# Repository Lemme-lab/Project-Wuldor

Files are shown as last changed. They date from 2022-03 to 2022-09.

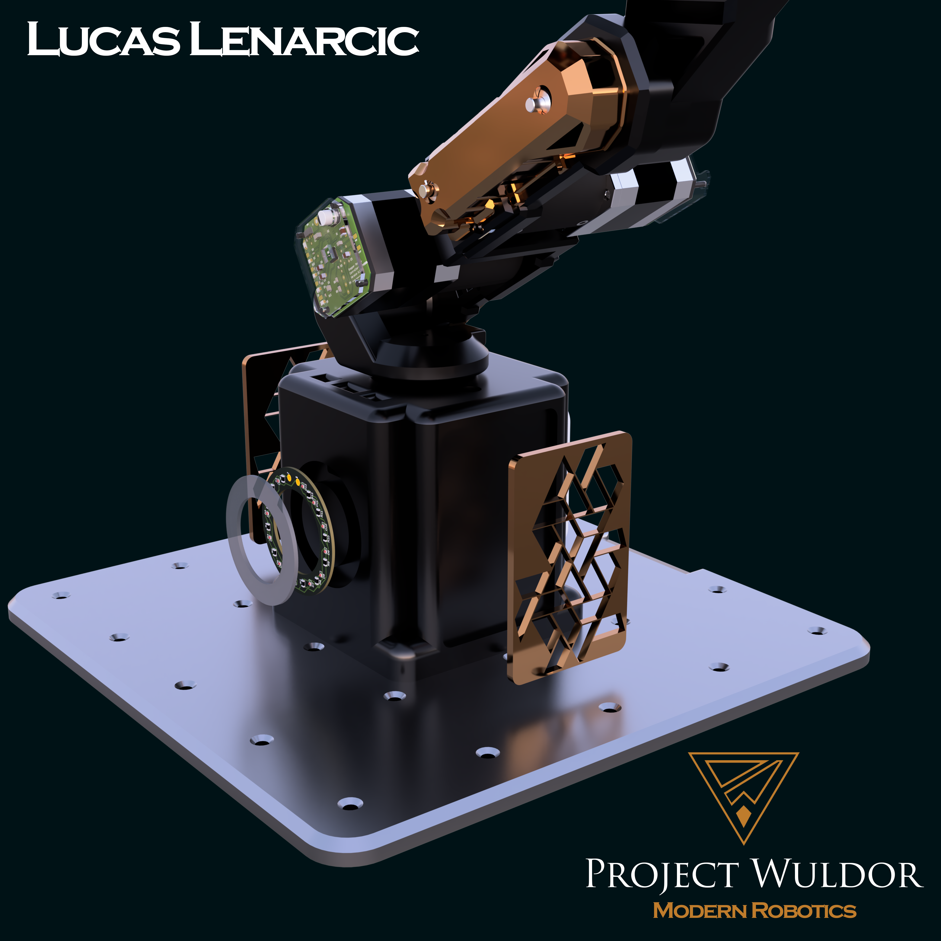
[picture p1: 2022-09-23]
Images/Assembly Led Ring - Base.png

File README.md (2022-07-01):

# Project Wuldor
---
## A completely custom 6 Axis Roboter-Arm (Still in progress) that won the 2022 HTL Mössingerstraße Technicus Award. 
---

---
Banner
---
unnamed
---
Packaging_Arm
---
Packaging_PCB's
---
PCB-Display
---

---
3D-Modell_2022-Mar-06_03-12-34PM-000_CustomizedView13790056020_mp4 (1)
---

## Features 
- Self Designed Stepper Motor Controller (A4988) 
- Self designed Main Controller with a small footprint
- Compact Size Factor
- Esthetic 
- Many other little Features

---
Main_PCB_Renders
---
Stepper_motors_driver_renders
---

## Planned Code:
### General:  
A few bullet points and explanations for the code part. Different technologies and programming languages such as C++, WEB-Dev, and Flutter will be used. It will go from Basic C and register manipulation to UI-Development on Cross-Platform Mobile Apps.  
  
- Controlling Axis 1- 5  
- Save Control sequence  
- Remote  Connection  
- Desktop  Application  
- Website  
- Mobile App  
- PHP Database  
- C++, HTML, CSS, JS, FLUTTER, JAVA, Python
- Tensorflow, Keras

---
  
### Website:  
An HTML Website that must be functional and appealing to use. Features will be send via a ESP32 and the included Wireless module. Cross-platform Data will mean that we will have to save the current data and inputs on a small database. UI and other Features will mean that we have to use JS with or without an additional framework.  
 --- 
Website-Wuldor
 --- 
- Checking Power Status  
- Check Wireless Connection  
- Current Voltage/Power Levels  
- Slider  Controlls for Motors  
- Test Motor func  
- Switch Mode (Normal Control, Train ,AI)  
- Cam Live Stream implementation  
- Stop/Start/hold -->pan> Slide buttons  
- Speed  
- Axis coordinates  
  
--- 
  
### Desktop Client  
A C++ or Java desktop client to be used when wired up to the robot arm. From the User ready interface to debbuging, testing and programming features will be included. This is one of the most important interface to the robot arm and as such it will be programmed first.  
  
- Checking Power Status  
- Check Wireless Connection  
- Current Voltage/Power Levels  
- Slider  Controlls for Motors  
- Test Motor func  
- Switch Mode (Normal Control,AI)  
- Cam  
- Debug Features / Console  
- Test  Features  
- Stop/Start/Hold -->  slidebuttons  
- Speed  
  
--- 
  
### Mobile Client  
Last we will do a Mobile Client app for controlling and checking the robot arm on the go. It will be programmed in Flutter or another Mobile Cross Platform Developer Kit.
--- 
  App-Prototype
---   
- Checking Power Status  
- Check Wireless Connection  
- Current-Voltage/Power Levels  
- Settings  
- Live Cam   

---

### Self-Test
Testclasses to exclude code-mistakes. Motors are working in the corract way and also the remote connection and controlling from the web applicatio, if so then we can put everything together and test the whole thing

- Motor
- Remote Connection
- Connections Seriell/Connectors 
  
---
### Currently in Work
---
IN_WORK
---
The whole code will be versioned via GIT, inputs to the Roboter Arm tested, and the whole project will be publicly available on GitHub.
---
https://trello.com/b/jWCULnX8
---

## Stepper Motor + Reducer
17HS4401 v4
---
17HS15-1684S-HG100 v7
---
11HS20-0674S-PG51 v3

------

## Stepper Motor Controller 

------

------

------
SteppperController pdf_v1_2022-Apr-15_08-58-34AM-000_CustomizedView13134334629_png_alpha
SteppperController pdf_v1_2022-Apr-15_08-48-39AM-000_CustomizedView932799733_png_alpha
------

## Main Controller

------

------
Main_Controller pdf_2022-Apr-15_07-07-20AM-000_CustomizedView21684845978_png_alpha
Main_Controller pdf_2022-Apr-15_07-34-52AM-000_CustomizedView14152361556_png_alpha
------
3D-Modell_2022-Jan-30_05-11-22PM-000_CustomizedView10729507097_png_alpha

------

## Roboter-Arm
---
Assemlby Bottom
---
Assembly Arm 2
---
Assembly Gripper
---
View Arm 3-4-5
---
Assembly Led Ring - Base
---

------

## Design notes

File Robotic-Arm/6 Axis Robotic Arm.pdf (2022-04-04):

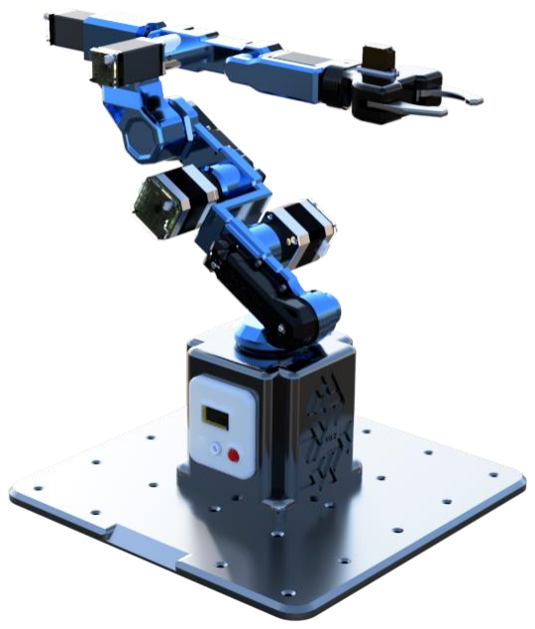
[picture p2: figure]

NAME | Lucas-Elias Lenarcic | STUNDEN | GEFEHLT
KLASSE | | DATUM
WERKSTÄTTE | | KAL. WOCHE
LEHRER | Prof. Grabner Burkhard | SEITE | GEPRÜFT

# 6 Axis Robotic Arm Technicus Award '22

### GitHub: https://github.com/Lemme-lab/Robotic-Arm

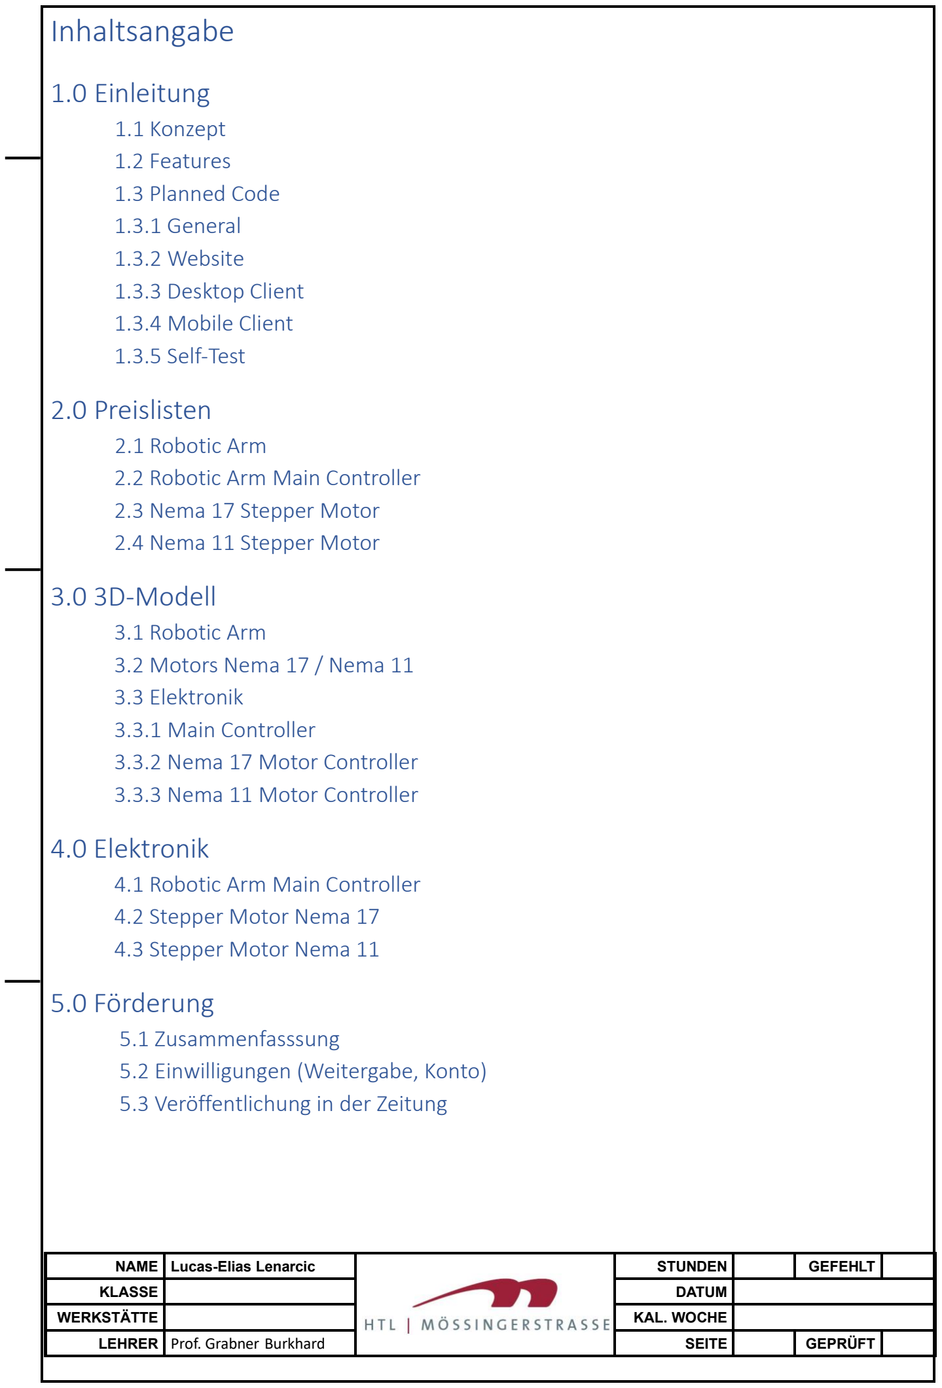
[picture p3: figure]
KLASSE; DATUM; WERKSTÄTTE; KAL. WOCHE; Inhaltsangabe; 1.0 Einleitung; 1.1 Konzept 1.2 Features 1.3 Planned Code 1.3.1 General 1.3.2 Website 1.3.3 Desktop Client 1.3.4 Mobile Client 1.3.5 Self-Test; 2.0 Preislisten; 2.1 Robotic Arm 2.2 Robotic Arm Main Controller 2.3 Nema 17 Stepper Motor 2.4 Nema 11 Stepper Motor; 3.0 3D-Modell; 3.1 Robotic Arm 3.2 Motors Nema 17 / Nema 11 3.3 Elektronik 3.3.1 Main Controller 3.3.2 Nema 17 Motor Controller 3.3.3 Nema 11 Motor Controller; 4.0 Elektronik; 4.1 Robotic Arm Main Controller 4.2 Stepper Motor Nema 17 4.3 Stepper Motor Nema 11; 5.0 Förderung; 5.1 Zusammenfasssung 5.2 Einwilligungen (Weitergabe, Konto) 5.3 Veröffentlichung in der Zeitung

NAME | Lucas-Elias Lenarcic | STUNDEN | GEFEHLT

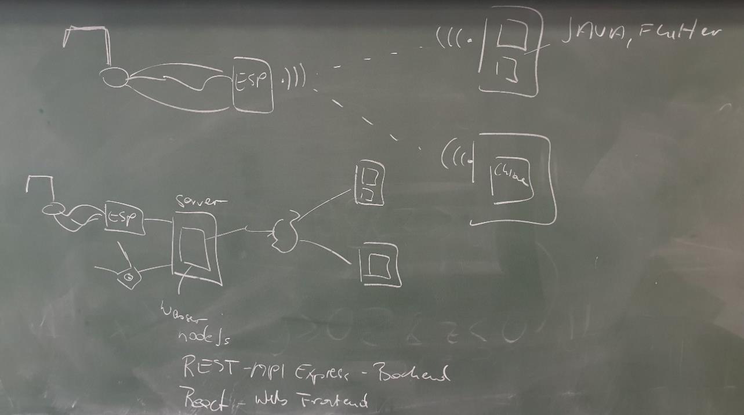
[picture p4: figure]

NAME | Lucas-Elias Lenarcic | STUNDEN | GEFEHLT
KLASSE | | DATUM
WERKSTÄTTE | | KAL. WOCHE

## 1.0 Einleitung

1.1 Konzept
Für den Technicus Award der HTL, haben wir (Lucas Lenarcic und Matteo Müller) uns,
im Zuge des Werkstättenunterrichts bei Herrn Prof. Grabner Burkhard, überlegt einen 6-Achsen Roboterarm zu bauen.

Der Roboterarm wurde/wird mithilfe von Fusion entworfen. Die einzelnen mechanischen Komponenten des Armgehäuses werden mithilfe eines 3D-Druckers gefertigt. Elektronische Komponenten, wie Motortreiber, Stromversorgung, Steuerung via App oder Web wurden/werden mit der PCB-Design Software Altium entworfen. Für die Herstellung dieser Platinen wird entweder die schulinterne Leiterplattenfertigung hinzugezogen oder ein externer Hersteller.

Es ist geplant mit dem Greifer des Roboterarms Objekte aufzuheben und diese an einem beliebigen, in der Reichweite des Armes gelegenen, Punkt wieder abzulegen.
Die Steuerung soll wie in den folgenden Punkten noch genauer beschrieben über mehrere Varianten möglich gemacht werden.

So soll man den Roboter mithilfe einer Webapplikation, also über eine selbst designte HTML-Website (virtueller Joystick, …) und folglich mit dem ESP32 und dessen eingebautem WLAN-Modul steuern können.
Die andere Variante wäre bzw. ist eine App, die wir mithilfe von Flutter designen werden.

NAME | Lucas-Elias Lenarcic | STUNDEN | GEFEHLT
KLASSE | | DATUM
WERKSTÄTTE | | KAL. WOCHE

1.2 Features

- Self Designed Stepper Motor Controller (A4988)
- Self designed Main Controller with a small footprint
- Compact Size Factor
- Esthetic
- Many other little Features

1.3 Planned Code:
1.3.1 General:
A few bullet points and explanations for the code part. Different technologies and programming languages such as C++, WEB-Dev, and Flutter will be used. It will go from Basic C and register manipulation to UI-Development on Cross-Platform Mobile Apps.
- Controlling Axis 1- 5
- Save Control sequence
- Remote Connection
- Desktop Application
- Website
- Mobile App
- PHP Database
- C++, HTML, CSS, JS, FLUTTER, JAVA, Python
- Tensorflow, Keras

NAME | Lucas-Elias Lenarcic | STUNDEN | GEFEHLT
KLASSE | | DATUM
WERKSTÄTTE | | KAL. WOCHE

1.3.2 Website:
A HTML Website that must be functional and appealing to use. Features will be send via a ESP32 and the included Wireless module. Cross-platform Data will mean that we will have to save the current data and inputs on a small database. UI and other Features will mean that we have to use JS with or without an additional framework.
- Checking Power Status
- Check Wireless Connection
- Current Voltage/Power Levels
- Slider Controlls for Motors
- Test Motor func
- Switch Mode (Normal Control, Train ,AI)
- Cam Live Stream implementation
- Stop/Start/hold -->pan> Slide buttons
- Speed
- Axis coordinates

1.3.3 Desktop Client
A C++ or Java desktop client to be used when wired up to the robot arm. From the User ready interface to debbuging, testing and programming features will be included. This is one of the most important interface to the robot arm and as such it will be programmed first.
- Checking Power Status
- Check Wireless Connection
- Current Voltage/Power Levels
- Slider Controlls for Motors
- Test Motor func
- Switch Mode (Normal Control,AI)
- Cam
- Debug Features / Console
- Test Features
- Stop/Start/Hold --> slidebuttons
- Speed

NAME | Lucas-Elias Lenarcic | STUNDEN | GEFEHLT
KLASSE | | DATUM
WERKSTÄTTE | | KAL. WOCHE

1.3.4 Mobile Client
Last we will do a Mobile Client app for controlling and checking the robot arm on the go. It will be programmed in Flutter or another Mobile Cross Platform Developer Kit.
- Checking Power Status
- Check Wireless Connection
- Current-Voltage/Power Levels
- Settings
- Live Cam

1.4.5 Self-Test
Testclasses to exclude code-mistakes. Motors are working in the corract way and also the remote connection and controlling from the web applicatio, if so then we can put everything together and test the whole thing
- Motor
- Remote Connection
- Connections Seriell/Connectors

## 2.0 Preislisten

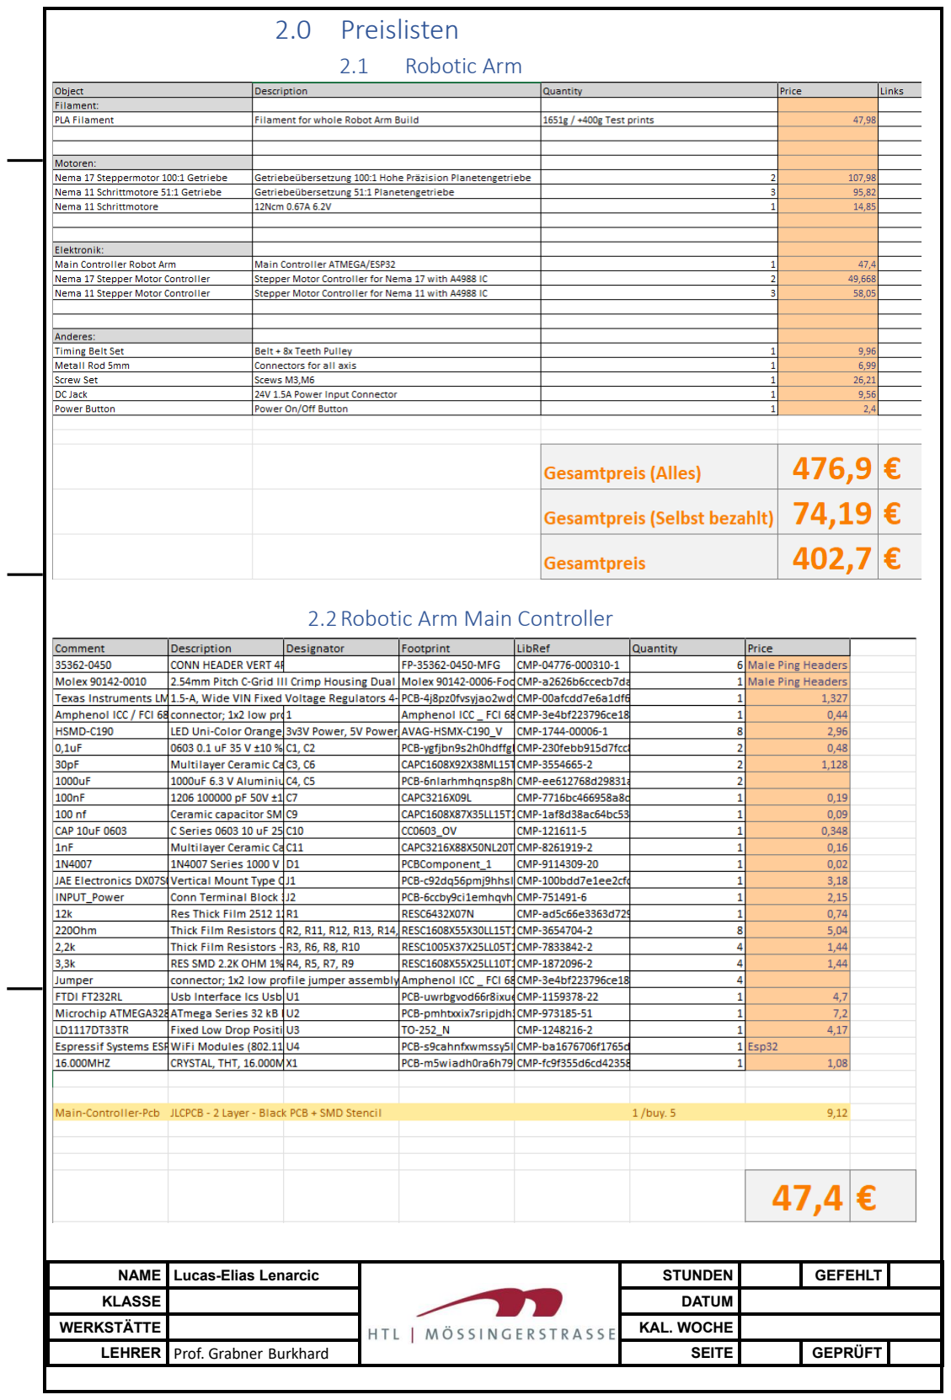
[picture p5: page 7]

NAME | Lucas-Elias Lenarcic | STUNDEN | GEFEHLT
KLASSE | | DATUM
WERKSTÄTTE | | KAL. WOCHE
2.1 | Robotic Arm

2.2Robotic Arm Main Controller

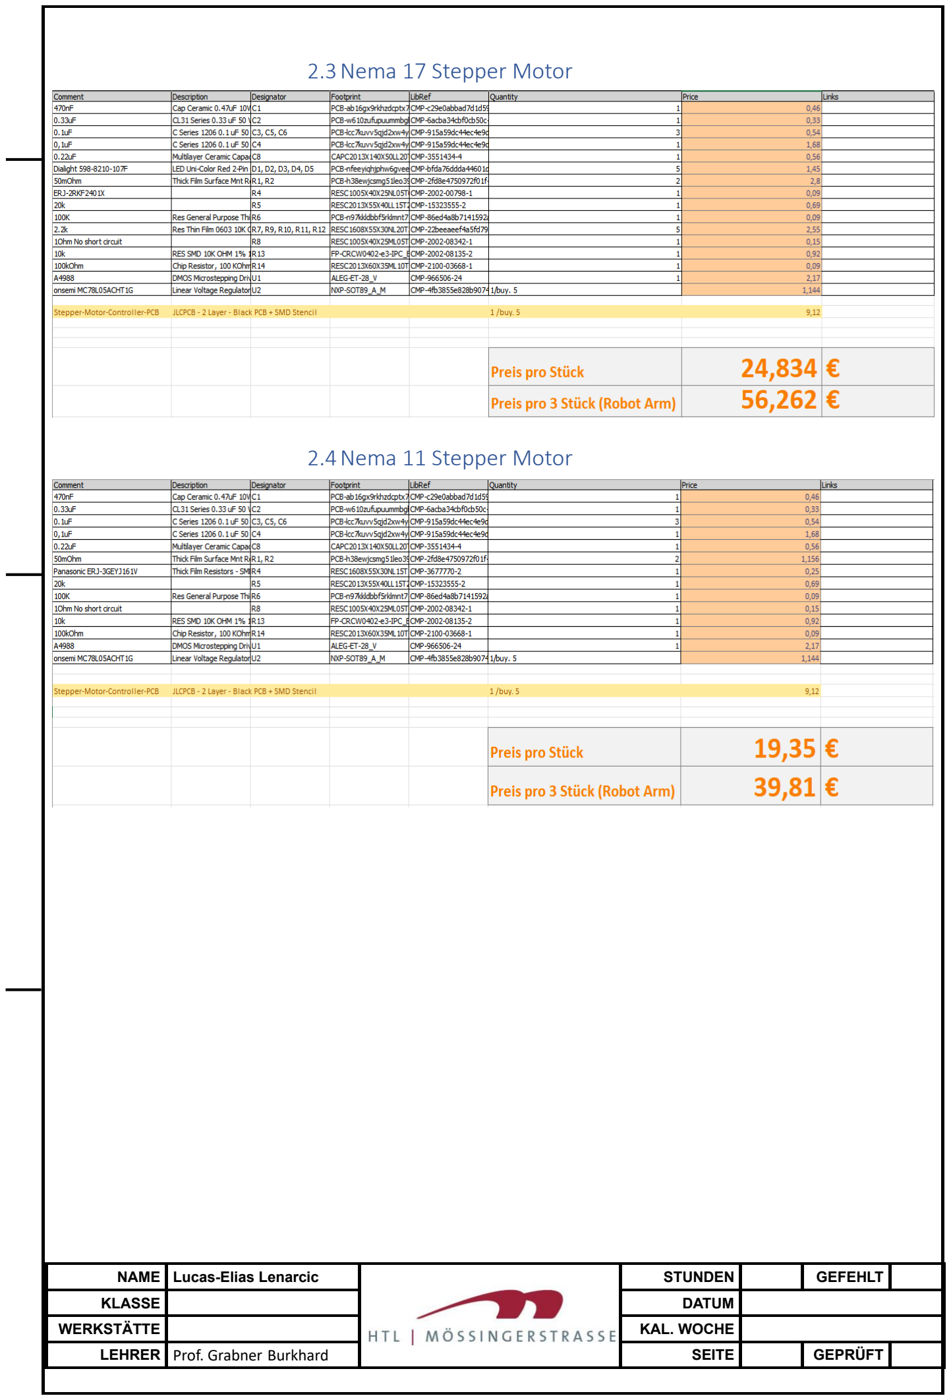
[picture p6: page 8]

NAME | Lucas-Elias Lenarcic | STUNDEN | GEFEHLT
KLASSE | | DATUM
WERKSTÄTTE | | KAL. WOCHE

2.3Nema 17 Stepper Motor

2.4Nema 11 Stepper Motor

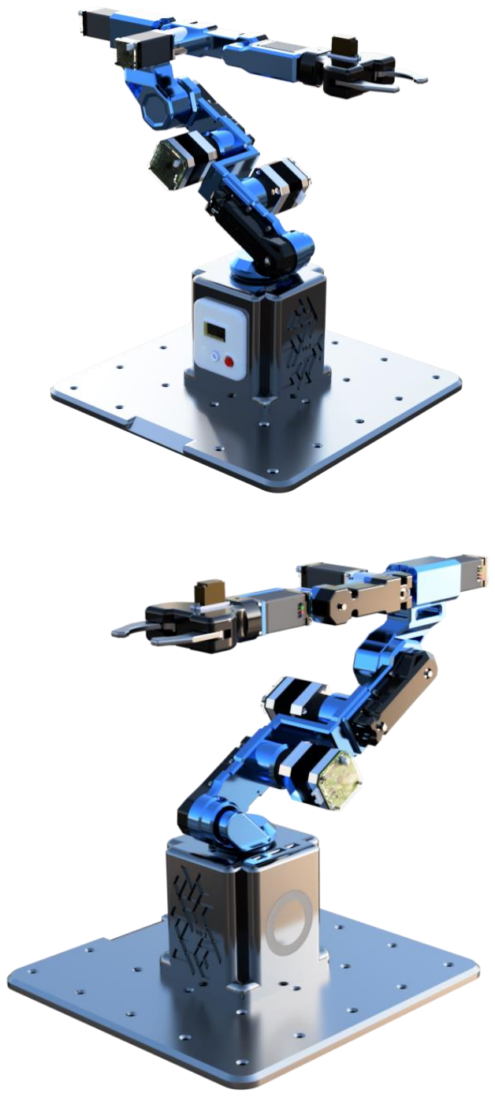
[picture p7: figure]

NAME | Lucas-Elias Lenarcic | STUNDEN | GEFEHLT
KLASSE | | DATUM
WERKSTÄTTE | | KAL. WOCHE

## 3.0 3D-Modells

3.1 Robotic Arm

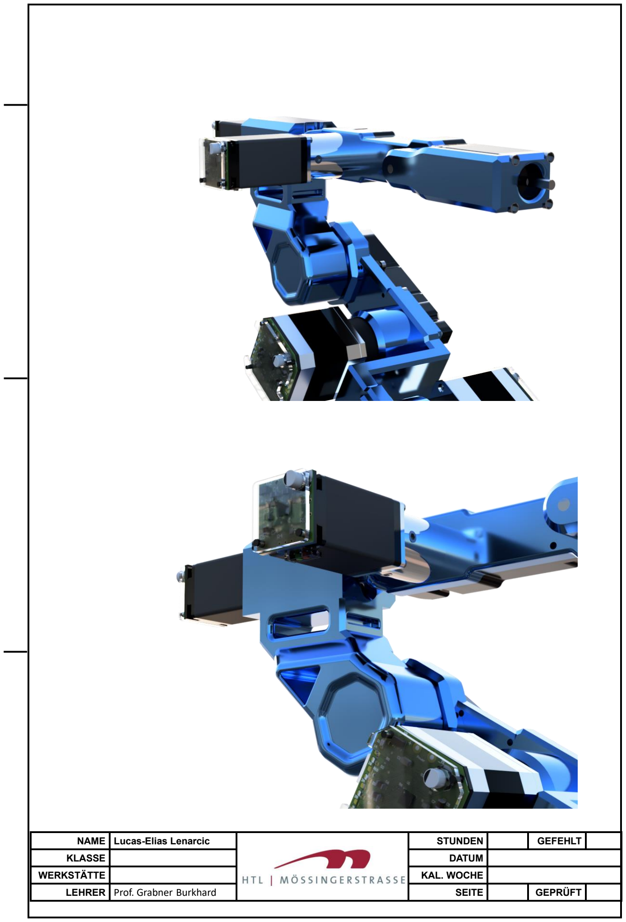
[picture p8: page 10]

NAME | Lucas -Elias Lenarcic | STUNDEN | GEFEHLT
KLASSE | | DATUM
WERKSTÄTTE | | KAL. WOCHE

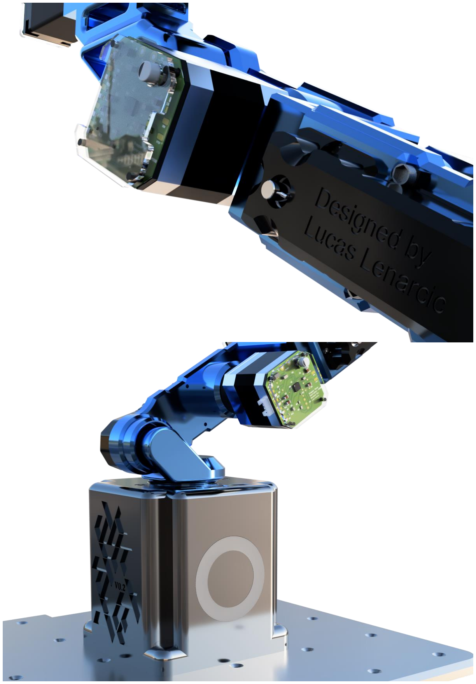
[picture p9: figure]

NAME | Lucas -Elias Lenarcic | STUNDEN | GEFEHLT
KLASSE | | DATUM
WERKSTÄTTE | | KAL. WOCHE

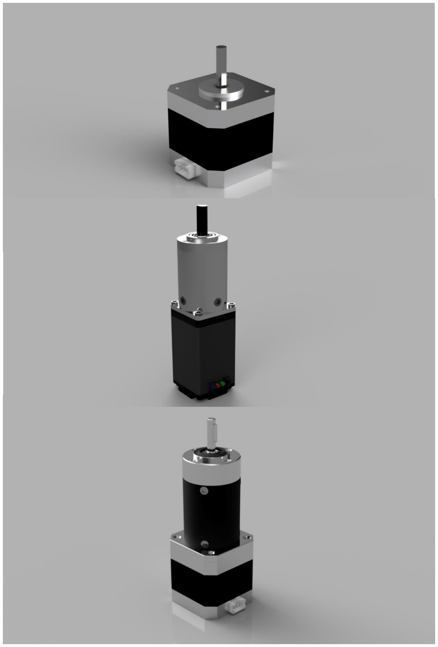
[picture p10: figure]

NAME | Lucas-Elias Lenarcic | STUNDEN | GEFEHLT
KLASSE | | DATUM
WERKSTÄTTE | | KAL. WOCHE

3.2 Motors Nema 17 / Nema 11

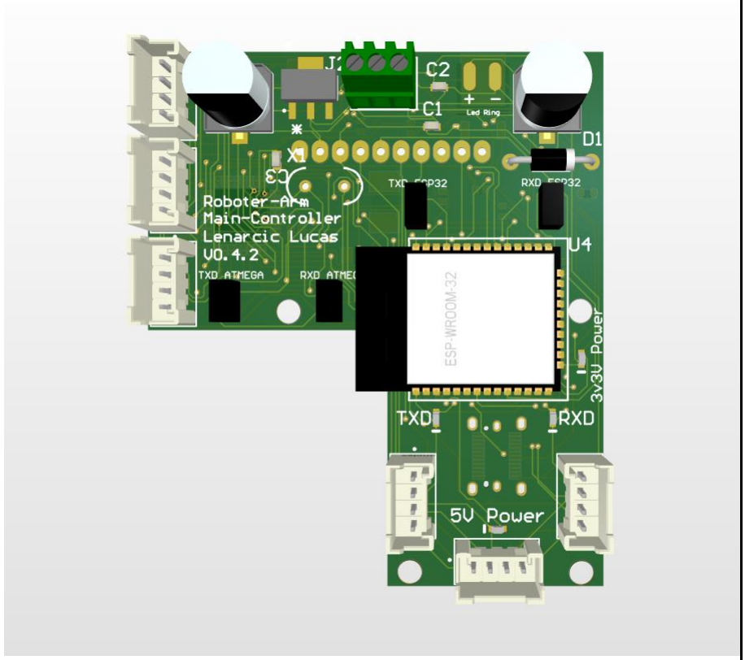
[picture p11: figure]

NAME | Lucas-Elias Lenarcic | STUNDEN | GEFEHLT
KLASSE | | DATUM
WERKSTÄTTE | | KAL. WOCHE

3.3Elektronik
3.3.1 Main Controller:

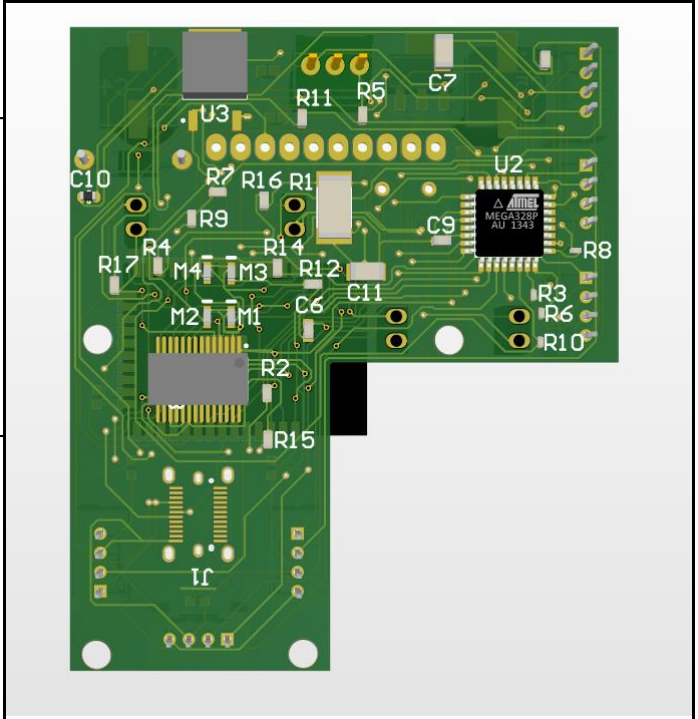
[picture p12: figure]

NAME | Lucas -Elias Lenarcic | STUNDEN | GEFEHLT
KLASSE | | DATUM
WERKSTÄTTE | | KAL. WOCHE

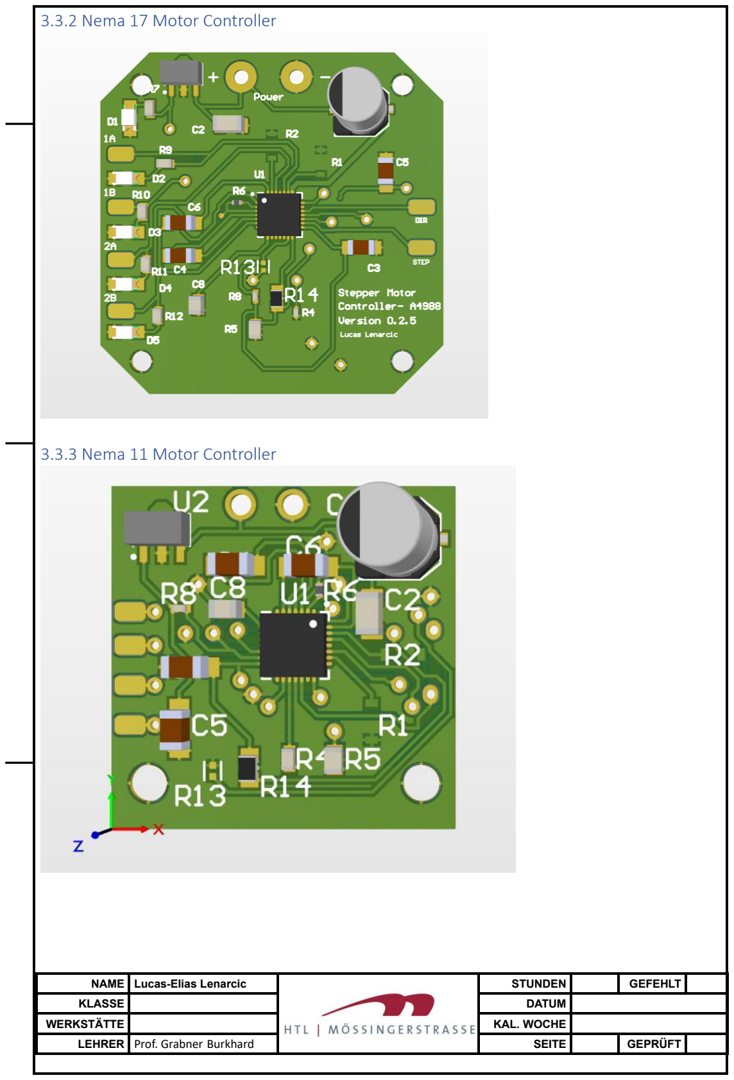
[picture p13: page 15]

NAME | Lucas-Elias Lenarcic | STUNDEN | GEFEHLT
KLASSE | | DATUM
WERKSTÄTTE | | KAL. WOCHE

3.3.2 Nema 17 Motor Controller

3.3.3 Nema 11 Motor Controller

## 4.0 Elektronik

## 4.1 Robotic Arm Main Controller

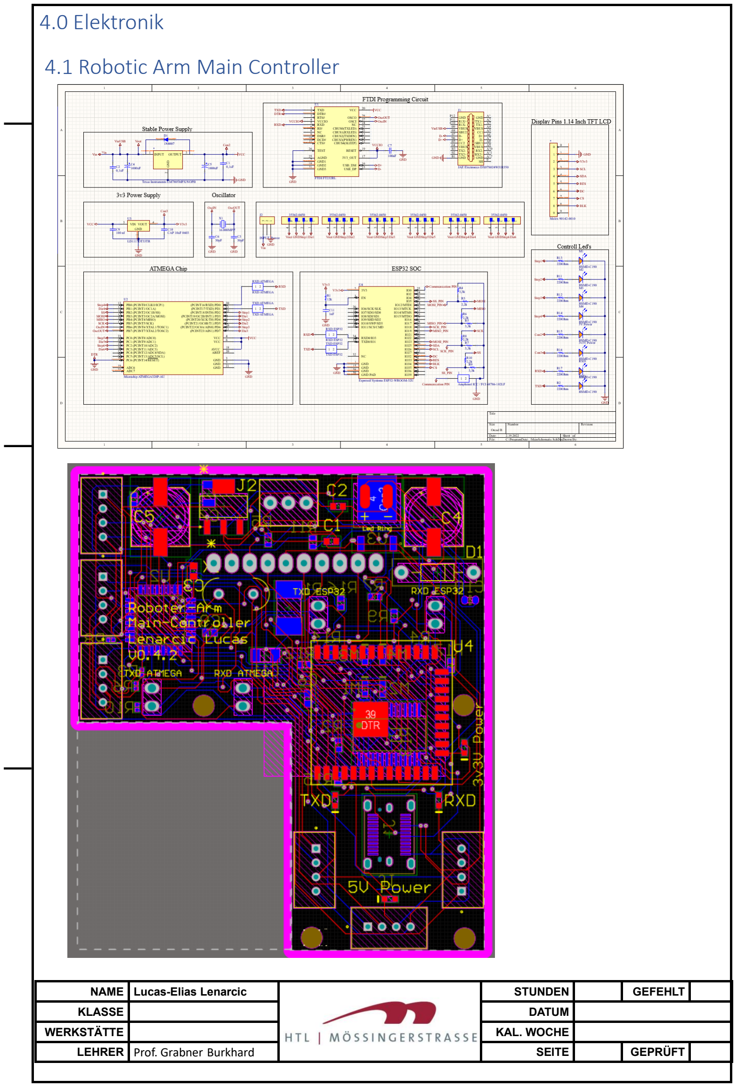
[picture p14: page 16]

NAME | Lucas-Elias Lenarcic | STUNDEN | GEFEHLT
KLASSE | | DATUM
WERKSTÄTTE | | KAL. WOCHE

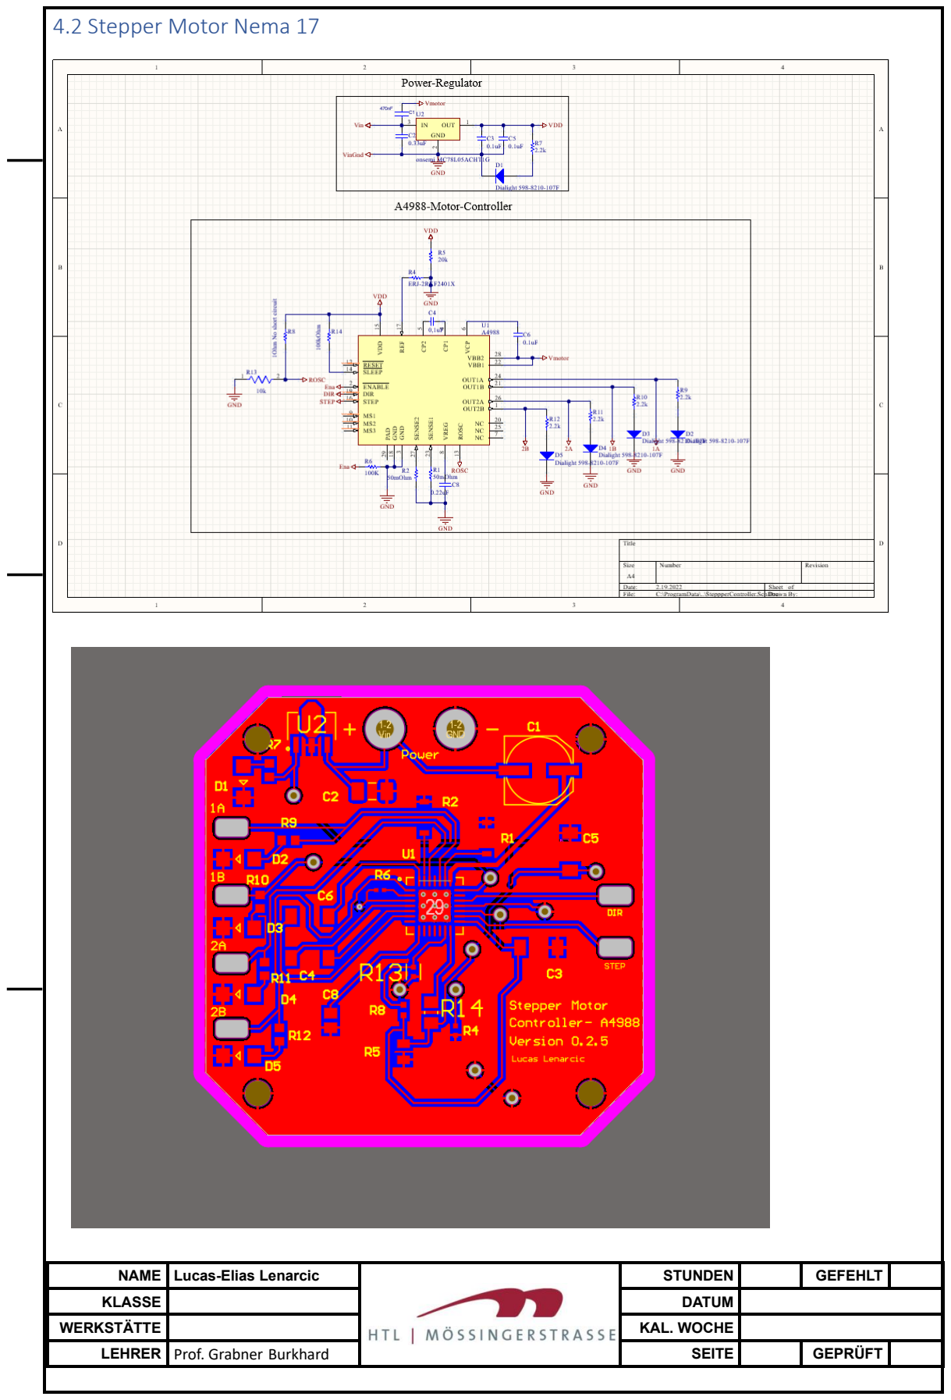
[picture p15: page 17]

NAME | Lucas-Elias Lenarcic | STUNDEN | GEFEHLT
KLASSE | | DATUM
WERKSTÄTTE | | KAL. WOCHE

4.2 Stepper Motor Nema 17

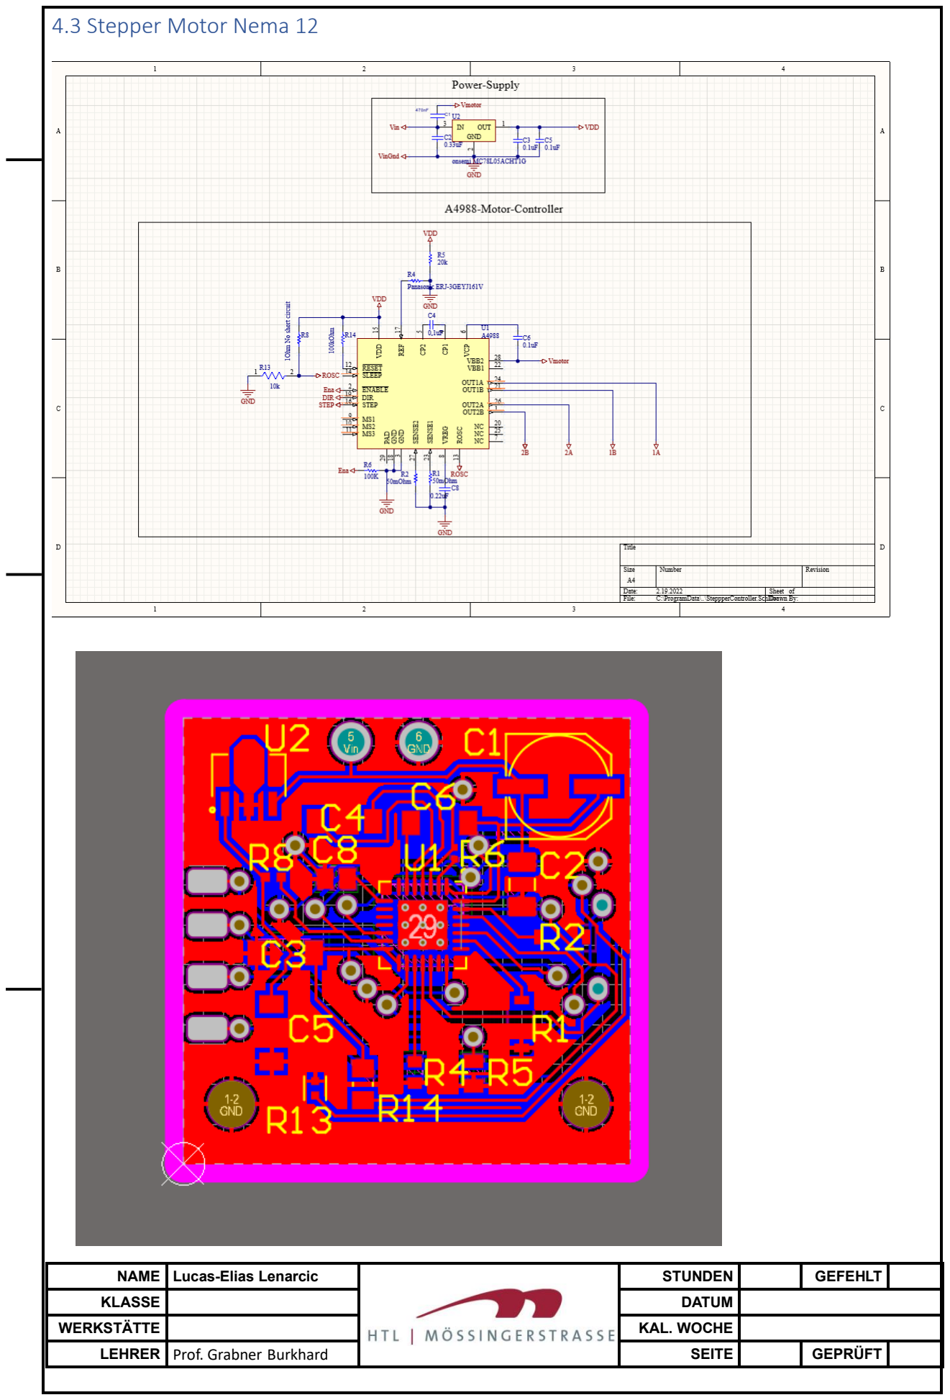
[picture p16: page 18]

NAME | Lucas-Elias Lenarcic | STUNDEN | GEFEHLT
KLASSE | | DATUM
WERKSTÄTTE | | KAL. WOCHE

4.3 Stepper Motor Nema 12

NAME | Lucas-Elias Lenarcic | STUNDEN | GEFEHLT
KLASSE | | DATUM
WERKSTÄTTE | | KAL. WOCHE

## 5.0 Förderung

5.1 Zusammenfasssung

Für den Technicus Award der HTL, haben wir (Lucas Lenarcic und Matteo Müller) uns,
im Zuge des Werkstättenunterrichts bei Herrn Prof. Grabner Burkhard, überlegt einen 6-Achsen Roboterarm zu bauen.

Der Roboterarm wurde/wird mithilfe von Fusion entworfen. Die einzelnen mechanischen Komponenten des Armgehäuses werden mithilfe eines 3D-Druckers gefertigt. Elektronische Komponenten, wie Motortreiber, Stromversorgung, Steuerung via App oder Web wurden/werden mit der PCB-Design Software Altium entworfen. Für die Herstellung dieser Platinen wird entweder die schulinterne Leiterplattenfertigung hinzugezogen oder ein externer Hersteller.

Es ist geplant mit dem Greifer des Roboterarms Objekte aufzuheben und diese an einem beliebigen, in der Reichweite des Armes gelegenen, Punkt wieder abzulegen.
Die Steuerung soll wie in den folgenden Punkten noch genauer beschrieben über mehrere Varianten möglich gemacht werden.

So soll man den Roboter mithilfe einer Webapplikation, also über eine selbst designte HTML-Website (virtueller Joystick, …) und folglich mit dem ESP32 und dessen eingebautem WLAN-Modul steuern können. Die andere Variante wäre bzw. ist eine App, die wir mithilfe von Flutter designen werden.

- Self Designed Stepper Motor Controller (Nema 17, Nema 11) (A4988)
- Self designed Main Controller (ATMEGA, ESP32, USB-C Interface, Display, Power Reg.)
- Different Interfaces (Controlling)
- Compact size factor of Electronics and Modell
- Esthetic appealing Modells, Interfaces and Electronics
- Many other little Features

Website:
A HTML Website that must be functional and appealing to use. Features will be send via a ESP32 and the included Wireless module. Cross-platform Data will mean that we will have to save the current data and inputs on a small database. UI and other Features will mean that we have to use JS with or without an additional framework.

Desktop Client
A C++ or Java desktop client to be used when wired up to the robot arm. From the User ready interface to debbuging, testing and programming features will be included. This is one of the most important interface to the robot arm and as such it will be programmed first.

Mobile Client
Last we will do a Mobile Client app for controlling and checking the robot arm on the go. It will be programmed in Flutter or another Mobile Cross Platform Developer Kit.

NAME | Lucas-Elias Lenarcic | STUNDEN | GEFEHLT
KLASSE | | DATUM
WERKSTÄTTE | | KAL. WOCHE

Eine Erklärung des Antragstellers, wie oft bereits Förderungen beim ABSVB beantragt, und und an ihn ausgezahlt wurden.
- Es wurden keine Anträge vor diesem beantragt und es wurden dadurch auch keine Fördergelder ausgezahlt.

Die saldierten Rechnungen der getätigten Ausgaben (als Original ), bis zum zu fördernden Betrag sind beizulegen (Motto: Keine Förderung ohne bezahlte Rechnung)!.

- Die Bauteile werden erst bestellt, wenn uns Förderungen zu diesem Projekt zugesagt werden. Die Rechnungen werden dann sofort nachgereicht. Alle Preislisten sind beigelegt.

5.2 Einwilligungen (Weitergabe, Konto)

Die Erklärung, dass sie/er damit einverstanden ist, dass der ABSVB die Arbeit für eigene Zwecke verwendet und verwertet. Die Weitergabe an SchülervertreterInnen zur Vervielfältigungen wird ausdrücklich gestattet.

- Antragsteller: _____________________________

Bei mehreren VerfasserInnen eine schriftliche Erklärung aller VerfasserInnen, dass sie mit der Überweisung auf das genannte Konto einverstanden sind.

Ich Matteo Müller bin einverstanden das die Überweisung der Fördergelder auf das Bankkonto
IBAN: AT76 2070 6045 0053 5861 geht.
- Matteo Müller: _____________________________

5.3 Veröffentlichung in der Zeitung

Bei Förderung von Projekten / Arbeiten, ist für die Veröffentlichung in der Zeitung des ABSVBs ein Projektbericht mit projektbezogenem Bild beizulegen (Jeweils als Datei (*.doc, *.jpg), für die EDV mäßige Weiterverarbeitung)!

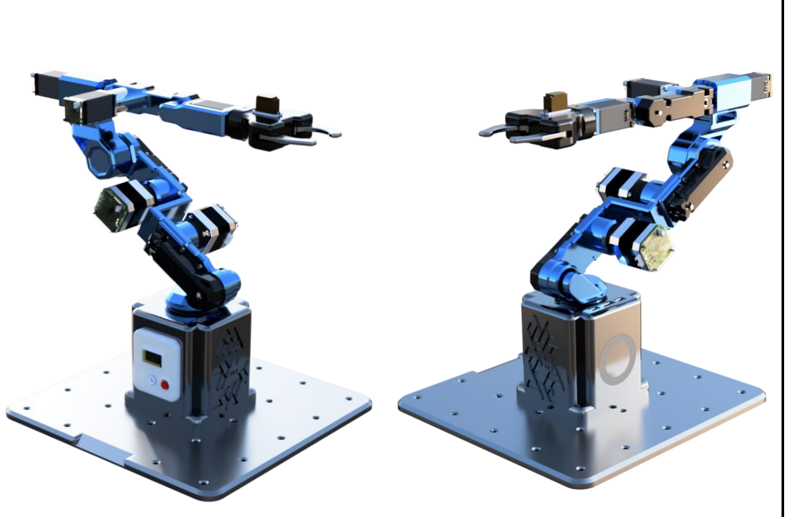
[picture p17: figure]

NAME | Lucas-Elias Lenarcic | STUNDEN | GEFEHLT
KLASSE | | DATUM
WERKSTÄTTE | | KAL. WOCHE

# Robotic-Arm Technicus Award

Für den Technicus Award der HTL, haben wir (Lucas Lenarcic und Matteo Müller) uns, im Zuge des Werkstättenunterrichts bei Herrn Prof. Grabner Burkhard, überlegt einen 6-Achsen Roboterarm zu bauen. Das Projekt wurde durch einen beträchtlich Teil vom Absolventenverband der HTL‘s Klagenfurt gefördert.

Alle Komponenten des Roboterarms werden/wurden von uns selbst entworfen. Me-chanische Bauteile wie das Gehäuse werden mittels 3D-Drucker gefertigt und die elektronischen Komponenten, sprich Platinen, mithilfe der Leiterplattenfertigung der Schule oder durch externe Hersteller.

Mit dem Greifer des Roboterarms soll man Objekte aufheben können und diese an einem beliebigen Punkt wieder ablegen.

Die Steuerung soll mithilfe einer Webapplikation, also über eine selbst designte HTML-Website (virtueller Joystick, …) und folglich mit dem ESP32 und dessen eingebautem WLAN-Modul steuerbar sein, ebenso ist eine Steuer-App geplant.

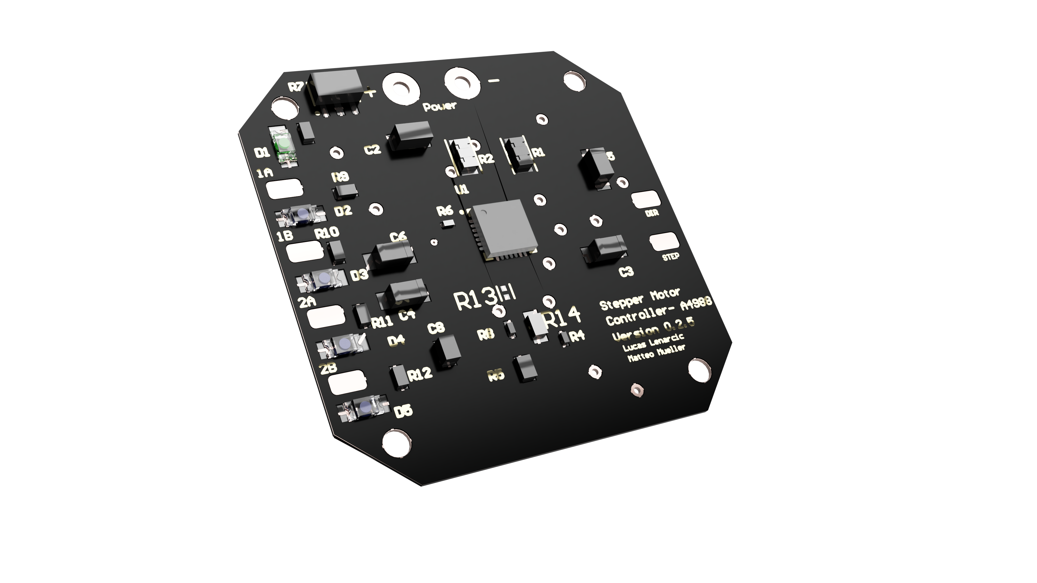
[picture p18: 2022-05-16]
Images/Stepper Controller 1.png

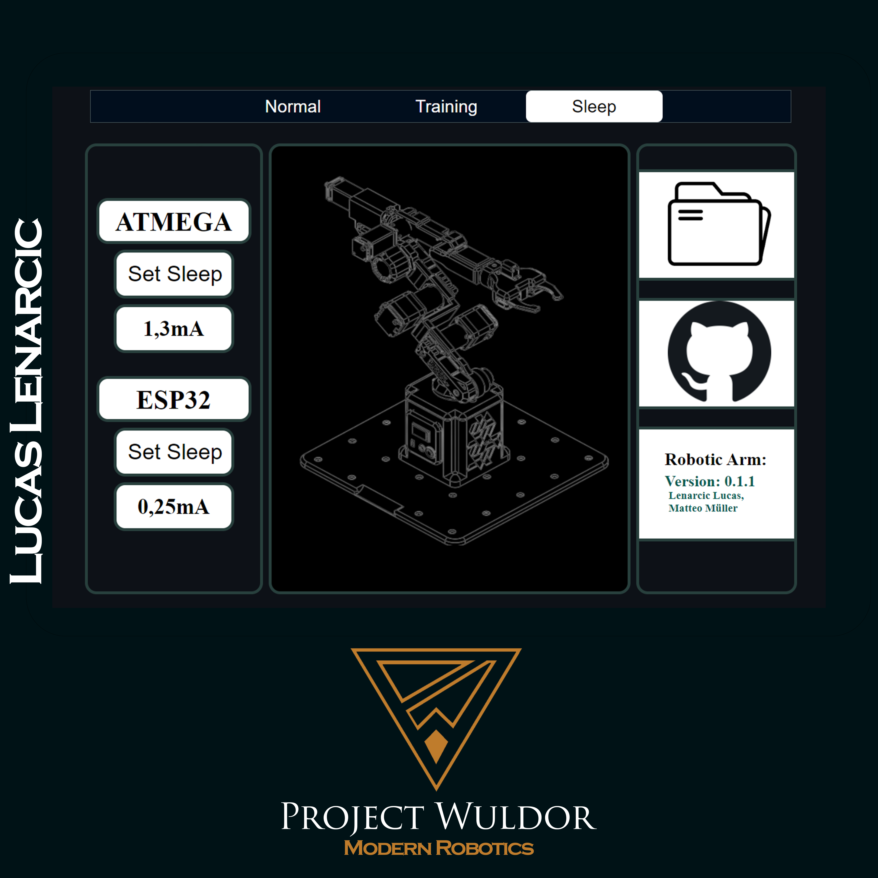
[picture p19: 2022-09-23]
Images/Website-Wuldor.png

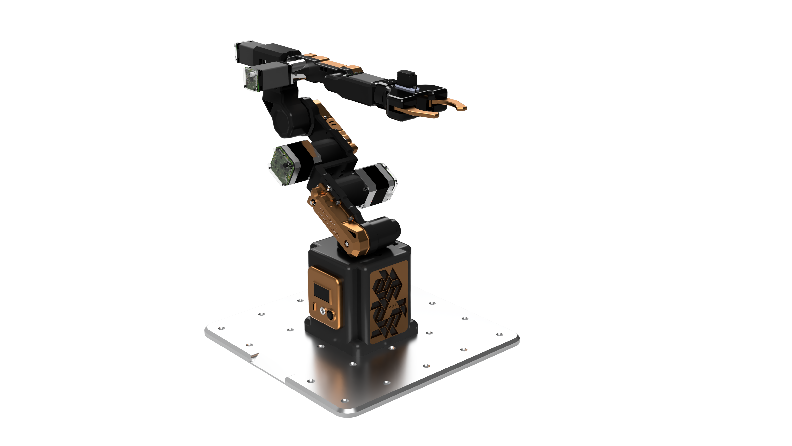
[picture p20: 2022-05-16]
Images/Modell-Copper.png

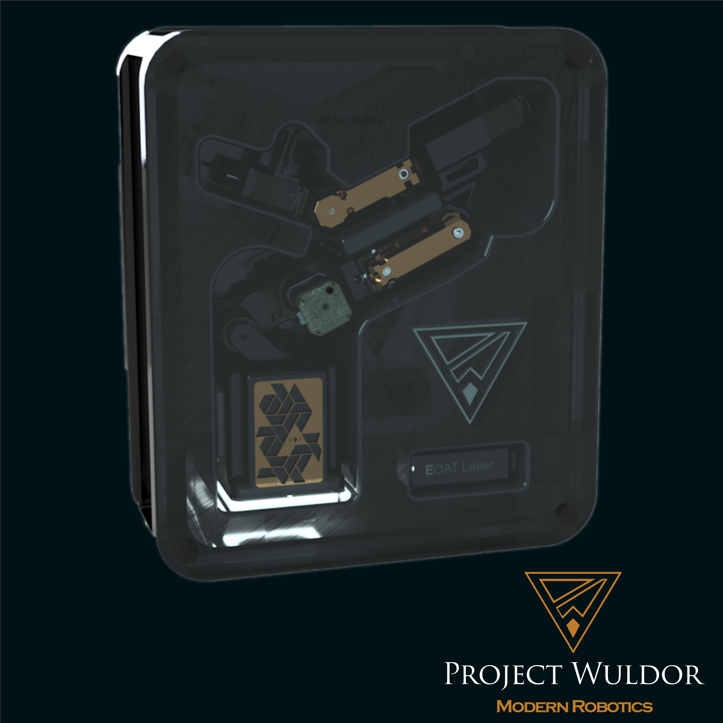
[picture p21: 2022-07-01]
Images/Packaging_Arm_2.png

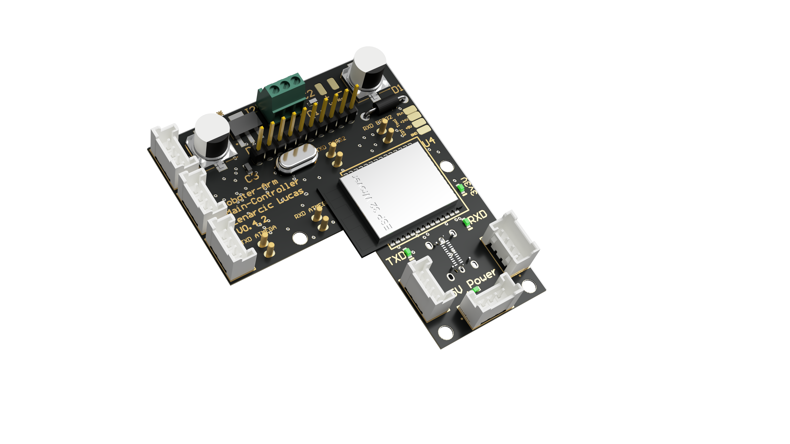
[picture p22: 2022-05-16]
Images/Main Controller 1.png

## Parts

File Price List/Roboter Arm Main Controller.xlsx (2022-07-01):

Comment | Description | Designator | Footprint | LibRef | Quantity
 | Resistance Weld Thru-Hole Crystal, 16 MHz, -20 to 70 degC, 2-Pin THD, RoHS, Bulk |  | FOX-FOXSLF160-20 | CMP-1749-00003-1 | 1
282836-2 | Female Header, Pitch 5 mm, 1 x 2 Position, Height 10 mm, Tail Length 3.5 mm, Rohs, Bulk |  | TECO-282836-2_V | CMP-1684-00017-1 | 1
LD1117DT33TR | Fixed Low Drop Positive Voltage Regulator, 3.3V, 3-Pin DPAK, Tape and Reel | +3V3 | TO-252_N | CMP-0244-00088-1 | 1
LM7805MPX/NOPB | IC REG LINEAR 5V 1.5A SOT223-4 | +5V | FP-LM7805MPX-NOPB-MFG | CMP-04917-000022-1 | 1
 | LED RED CLEAR 0805 SMD | 3V3 Power, 5V Power, EN, Miso, Mosi, RXD, SPI, Step1, Step2, Step3, Step4, TXD | FP-150080SS75000-MFG | CMP-1426-00010-2 | 12
ATmega328P-AU | 8-bit AVR Microcontroller, 32KB Flash, 1KB EEPROM, 2KB SRAM, 32-pin TQFP, Industrial Grade (-40°C to 85°C) | ATMEGA328P | 32A_M | CMP-0095-00269-2 | 1
 | Cap Ceramic 100nF 50V X7R 10% Pad SMD 0603 +125°C Automotive T/R | C1, C4, C5, C6, C9 | FP-CGA3E-0_3-0_1-IPC_A | CMP-2000-07546-2 | 5
 | Aluminum Electrolytic Capacitor, Low Impedance, 1000 uF +/- 20%, 16 V, -55 to 105 degC, 2-Pin 10.3 x 10.3 x 13.5 mm SMD, RoHS, Reel | C2, C3 | NIC-UCL-10x13.5-2_V | CMP-0926-00001-1 | 2
 | CAP CER 30PF 50V 5% NP0 0603 | C7, C8 | FP-C0603C-CF-MFG | CMP-1035-00914-3 | 2
1N4007 | Rectifier diode 1000 V 1 A DO-41, , | D1 | FP-1N4007-MFG | CMP-123542-000001-1 | 1
61300811121 | THT Vertical Pin Header WR-PHD, Pitch 2.54 mm, Single Row, 8 pins | Display | 61300811121 | CMP-1502-01076-1 | 1
ESP32-WROOM-32D | WIFI MODULE 32MBITS SPI FLASH | ESP-32 | FP-ESP32-WROOM-32D-MFG | CMP-194065-000003-1 | 1
FT232RL | IC USB FS SERIAL UART 28-SSOP | FT232RL | FTDI-SSOP-28_M | CMP-2000-05029-1 | 1
 | Male Header, Pitch 2 mm, 1 x 4 Position, Height 6 mm, Tail Length 3.4 mm, -25 to 85 degC, RoHS, Bulk | P1, P2, P3, P4, P5, P6 | JST-B4B-PH-K-S_V | CMP-2000-05165-1 | 6
MMBT2222A-7-F | TRANS NPN 40V 0.6A SMD SOT23-3 | Q1, Q2 | FP-SOT23-IPC_A | CMP-1693-00003-4 | 2
RC0402FR-073K3L |  | R1, R2, R3, R4, R18, R20 | RESC1005X40X25ML05T10 | CMP-2002-07652-1 | 6
RC0603FR-072K2L | Thick Film Resistor, 2.2 KOhm, 100 mW, 50 V, +/- 1%, -55 to 155 degC, 2-Pin SMD (0603), RoHS, Tape and Reel | R5, R6, R7, R8, R17, R19 | RESC1608X55X25LL10T15 | CMP-2000-06934-1 | 6
 | Chip Ferrite Bead, 0603, 220Ω @ 100MHz, 25%, 0.04Ω, 2.5A | R9, R10, R11, R12, R13, R14, R15, R16, R21, R22, R23, R27 | FP-BLM18-0_15-t0_5-MFG | CMP-0686-00596-3 | 12
ERJ3EKF1002V | Chip Resistor, 10 KOhm, +/- 1%, 0.1 W, -55 to 155 degC, 0603 (1608 Metric), RoHS, Tape and Reel | R24, R25 | RESC1609X55X30LL15T15 | CMP-1012-00623-3 | 2
CRCW060312K0FKEA | RES Thick Film, 12kΩ, 1%, 0.1W, 100ppm/°C, 0603 | R26 | FP-CRCW0603-e3-IPC_A | CMP-2000-03877-2 | 1
436333045822 | WS-TASU J-Bend J-Bend SMD Tact Switch with boss design 4.7X3.5 mm side push | Reset | 436333045822 | CMP-1464-00001-1 | 1
RXD ATMEGA | CONN HEADER VERT 2POS 2MM | RXD ATMEGA | FP-M22-2510205-MFG | CMP-15831-000005-1 | 1
RXD ESP32 | CONN HEADER VERT 2POS 2MM | RXD ESP | FP-M22-2510205-MFG | CMP-15831-000005-1 | 1
TXD ESP32 | CONN HEADER VERT 2POS 2MM | TXD ATMEGA, TXD ESP | FP-M22-2510205-MFG | CMP-15831-000005-1 | 2
DX07S024WJ1R350 | No Description Available | USB-C | CONN_DX07S024WJ1R350_JAE | DX07S024WJ1R350 | 1

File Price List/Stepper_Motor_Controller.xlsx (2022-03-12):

Comment | Description | Designator | Footprint | LibRef | Quantity | Price | Links
470nF | Cap Ceramic 0.47uF 10V X5R 20% SMD 0402 85°C T/R | C1 | PCB-ab16gx9rkhzdcptx7kd3-1 | CMP-c29e0abbad7d1d59-2 | 1 | 0.46 | https://www.digikey.at/en/products/detail/0402ZD474MAT2A/478-13018-1-ND/9948536?curr=usd
0.33uF | CL31 Series 0.33 uF 50 V ±10 % Tolerance X7R SMT Multilayer Ceramic Capacitor | C2 | PCB-w610zufupuummbghd1in-1 | CMP-6acba34cbf0cb50c-1 | 1 | 0.33 | https://www.digikey.at/de/products/detail/CL31B334KBFNNNE/1276-1138-1-ND/3889224?curr=eur
0.1uF | C Series 1206 0.1 uF 50 V ±5 % Tolerance C0G SMT Multilayer Ceramic Capacitor | C3, C5, C6 | PCB-lcc7kuvv5qjd2xw4yurg-1 | CMP-915a59dc44ec4e9d-4 | 3 | 0.54 | https://www.digikey.at/de/products/detail/C3216C0G1H104J160AA/445-7694-2-ND/2733129?curr=eur
0,1uF | C Series 1206 0.1 uF 50 V ±5 % Tolerance C0G SMT Multilayer Ceramic Capacitor | C4 | PCB-lcc7kuvv5qjd2xw4yurg-1 | CMP-915a59dc44ec4e9d-4 | 1 | 1.68 | https://www.digikey.at/de/products/detail/C3216C0G1H104J160AA/445-7694-2-ND/2733129?curr=eur
0.22uF | Multilayer Ceramic Capacitors MLCC - SMD/SMT 50volts .22uF 5% X7R 7inch reel | C8 | CAPC2013X140X50LL20T25 | CMP-3551434-4 | 1 | 0.56 | https://at.rs-online.com/web/p/keramik-vielschichtkondensatoren/1441425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
Dialight 598-8210-107F | LED Uni-Color Red 2-Pin Chip 1206(3216Metric) T/R | D1, D2, D3, D4, D5 | PCB-nfeeyiqhjphw6gveeqew-1 | CMP-bfda76ddda44601d-2 | 5 | 1.45 | https://www.digikey.at/de/products/detail/5988210107F/350-2047-2-ND/1291281?curr=eur
50mOhm | Thick Film Surface Mnt Resistor 2512 Case 50MOhm +/-1% 1W +/-100ppm/degC | R1, R2 | PCB-h38ewjcsmg51leo397rp-1 | CMP-2fd8e4750972f01f-1 | 2 | 2.8 | https://www.mouser.at/ProductDetail/Vishay-Dale/CRCW080550R0FKTA?qs=aRXG1QX2Yl9J6LSLM7CpJQ%3D%3D
ERJ-2RKF2401X |  | R4 | RESC1005X40X25NL05T05 | CMP-2002-00798-1 | 1 | 0.09 | https://www.digikey.at/en/products/detail/panasonic-electronic-components/ERJ-2RKF2401X/1746161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
20k |  | R5 | RESC2013X55X40LL15T20 | CMP-15323555-2 | 1 | 0.69 | https://www.digikey.at/de/products/detail/TNPW080520K0BEEA/TNP20.0KABCT-ND/1857107?curr=eur
100K | Res General Purpose Thick Film 0402 100k Ohm 1% 1/16W ±100ppm/°C Molded Paper T/R | R6 | PCB-n97kkldbbf5rklmnt71m-1 | CMP-86ed4a8b7141592a-1 | 1 | 0.09 | https://www.digikey.at/de/products/detail/CRGCQ0402F100K/A129651CT-ND/8577483?curr=eur
2.2k | Res Thin Film 0603 10K Ohm 0.5% 1/16W ±25ppm/°C Molded SMD SMD Paper T/R | R7, R9, R10, R11, R12 | RESC1608X55X30NL20T20 | CMP-22beeaeef4a5fd79-1 | 5 | 2.55 | https://www.digikey.at/en/products/detail/panasonic-electronic-components/ERA-2ARC222X/5140972
1Ohm No short circuit |  | R8 | RESC1005X40X25ML05T05 | CMP-2002-08342-1 | 1 | 0.15 | https://www.digikey.at/en/products/detail/rohm-semiconductor/KTR03EZPF1R00/2288554
10k | RES SMD 10K OHM 1% 1/16W 0402 | R13 | FP-CRCW0402-e3-IPC_B | CMP-2002-08135-2 | 1 | 0.92 | https://www.digikey.at/en/products/detail/te-connectivity-passive-product/352210KFT/5244971
100kOhm | Chip Resistor, 100 KOhm, +/- 1%, 0.125 W, -55 to 155 degC, 0805 (2012 Metric), RoHS, Tape and Reel | R14 | RESC2013X60X35ML10T20 | CMP-2100-03668-1 | 1 | 0.09 | https://www.digikey.at/de/products/detail/bourns-inc./CR0805-JW-104ELF/3925418
A4988 | DMOS Microstepping Driver with Translator and Overcurrent Protection, 3 to 5.5 V, -20 to 85 degC, 28-Pin QFN (ET), RoHS, Tape and Reel | U1 | ALEG-ET-28_V | CMP-966506-24 | 1 | 2.17 | https://at.farnell.com/allegro-microsystems/a4988settr-t/motor-driver-stepper-2a-qfn-28/dp/2057418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
onsemi MC78L05ACHT1G | Linear Voltage Regulator, 100 mA, 5 to 24 V, Positive Vout: 5.0 V; TJ = 0°C to +125°C | U2 | NXP-SOT89_A_M | CMP-4fb3855e828b9074-8 | 1/buy. 5 | 1.144 | https://at.farnell.com/on-semiconductor/mc78l05acht1g/lin-spannungsregler-5v-0-1a-sot/dp/2845173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
Stepper-Motor-Controller-PCB | JLCPCB - 2 Layer - Black PCB + SMD Stencil |  |  |  | 1 /buy. 5 | 9.12
 |  |  |  |  | Preis pro Stück | 24.834 | €
 |  |  |  |  | Preis pro 3 Stück (Robot Arm) | 56.262 | €

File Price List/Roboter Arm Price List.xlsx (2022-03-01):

Object | Description | Quantity | Price |  | Links
Filament:
PLA Filament |  | 1651g / +400g Test prints | 47.98 |  | https://www.amazon.de/gp/product/B07TJG7SX3/ref=ppx_yo_dt_b_asin_title_o07_s00?ie=UTF8&psc=1
Motoren:
Nema 17 Steppermotor 100:1 Getriebe | Getriebeübersetzung 100:1 Hohe Präzision Planetengetriebe | 2 | 107.98 |  | https://www.omc-stepperonline.com/de/nema-17-schrittmotore-l-39mm-getriebeubersetzung-100-1-hohe-prazision-planetengetriebe.html
Nema 11 Schrittmotore 51:1 Getriebe | Getriebeübersetzung 51:1 Planetengetriebe | 3 | 95.82 |  | https://www.omc-stepperonline.com/de/nema-11-schrittmotore-bipolar-l-51mm-w-getriebeubersetzung-51-1-planetengetriebe.html
Nema 11 Schrittmotore | 12Ncm 0.67A 6.2V | 1 | 14.85 |  | https://www.omc-stepperonline.com/de/nema-11-28mm-schrittmotor/nema-11-bipolar-1-8deg-12ncm-17oz-in-0-67a-6-2v-28x28x51mm-4-drahte.html
Elektronik:
Main Controller Robot Arm | Custom Designed Controller with ESP32, ATMEAG USB-C Interface | 1 | 47.4 |  | https://github.com/Lemme-lab/Robotic-Arm/blob/main/Price%20List/Roboter%20Arm%20Main%20Controller.xlsx
Nema 17 Stepper Motor Controller | Custom Designed Stepper Motor Controller on A4988 IC Nema 17 | 2 | 49.668 |  | https://github.com/Lemme-lab/Robotic-Arm/blob/main/Price%20List/Stepper_Motor_Controller.xlsx
Nema 11 Stepper Motor Controller | Custom Designed Stepper Motor Controller on A4988 IC Nema 11 | 3 | 58.05 |  | https://github.com/Lemme-lab/Robotic-Arm/blob/main/Price%20List/Stepper_Motor_Controller_Nema11.xlsx
Anderes:
Timing Belt Set | Belt + 8x Teeth Pulley | 1 | 9.96 |  | https://www.amazon.de/-/en/Dadabig-Printer-Timing-Pulley-Pieces/dp/B07XHRQ8H1
Metall Rod 5mm |  | 1 | 6.99 |  | https://www.amazon.de/-/en/sourcing-Round-Diameter-Length-Turning/dp/B07LBM311H
Screw Set |  | 1 | 26.21 |  | https://www.amazon.de/-/en/Jayzuum-Stainless-Washers-Assortment-Storage/dp/B091XZP6QS
DC Jack |  | 1 | 9.56 |  | https://www.amazon.de/-/en/RUNCCI-YUN-Adapter-Hollow-Surveillance-Cameras/dp/B089DXQDS9
Power Button |  | 1 | 2.4 |  | https://www.tme.eu/en/details/ps502mc-b/standard-switches/sci/r13-502-mc-05-0b/
 | Gesamtpreis (Alles) |  | 476.868 | €
 | Gesamtpreis (Selbst bezahlt) |  | 74.19 | €
 | Gesamtpreis |  | 402.678 | €

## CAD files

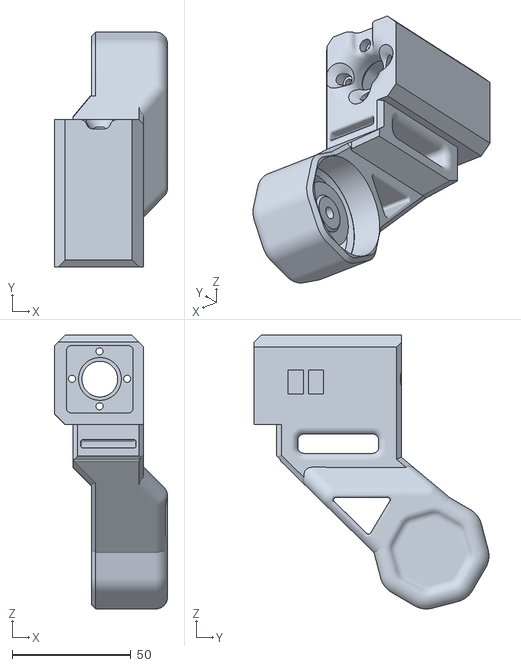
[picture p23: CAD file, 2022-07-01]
Robotic-Arm/Models/Arm3.stl
47.5 x 98.7 x 115.2

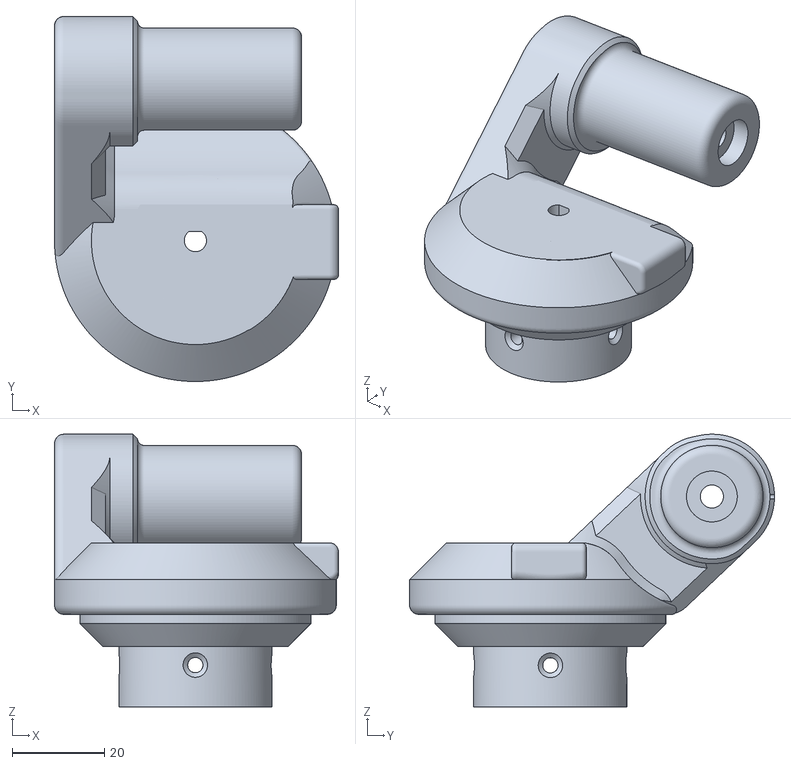
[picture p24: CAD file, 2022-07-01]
Robotic-Arm/Models/Arm1.stl
61.5 x 79.0 x 59.0

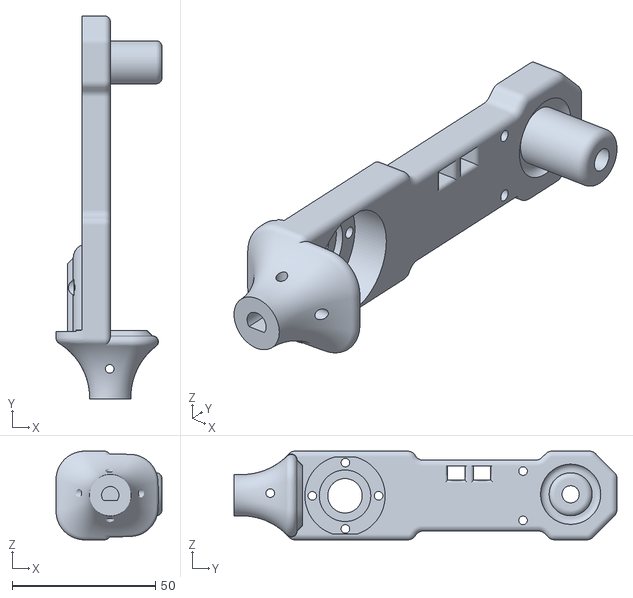
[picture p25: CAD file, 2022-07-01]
Robotic-Arm/Models/Arm4.stl
37.0 x 133.7 x 31.0

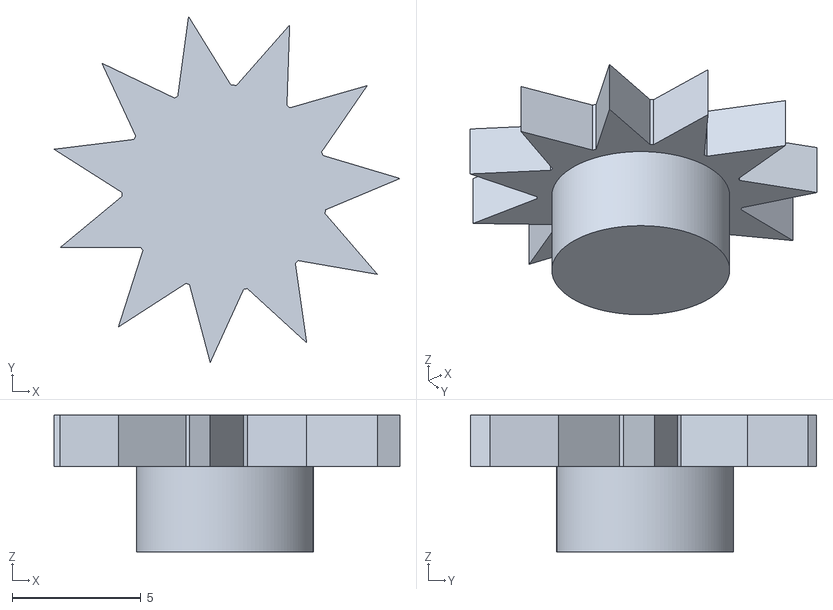
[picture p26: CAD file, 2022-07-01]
Robotic-Arm/Models/Gear2.stl
13.4 x 13.4 x 5.30

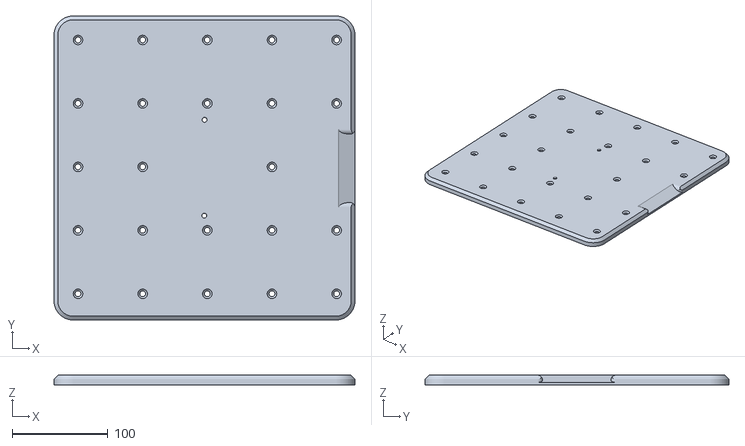
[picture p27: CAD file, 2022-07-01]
Robotic-Arm/Models/Ständer-Base.stl
314.3 x 317.4 x 10.0

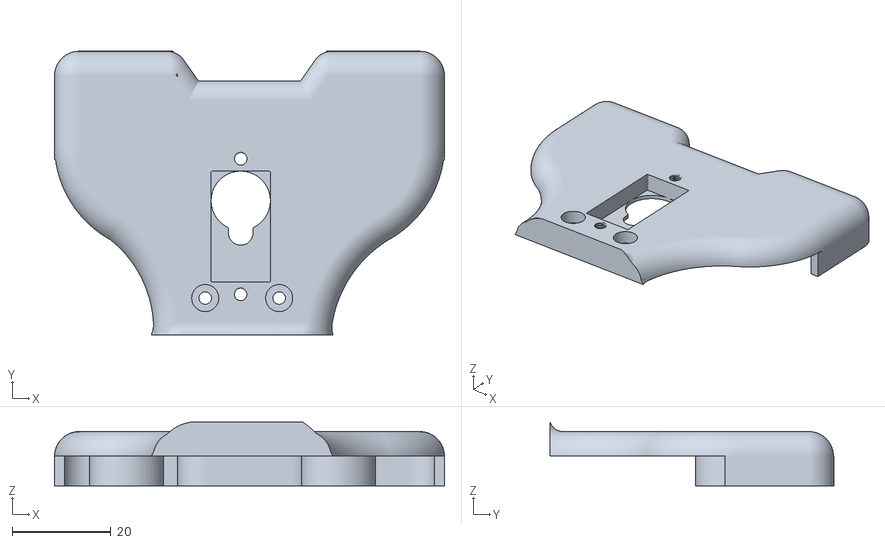
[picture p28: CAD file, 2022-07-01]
Robotic-Arm/Models/eoat_tool_cover.stl
79.1 x 57.5 x 12.9

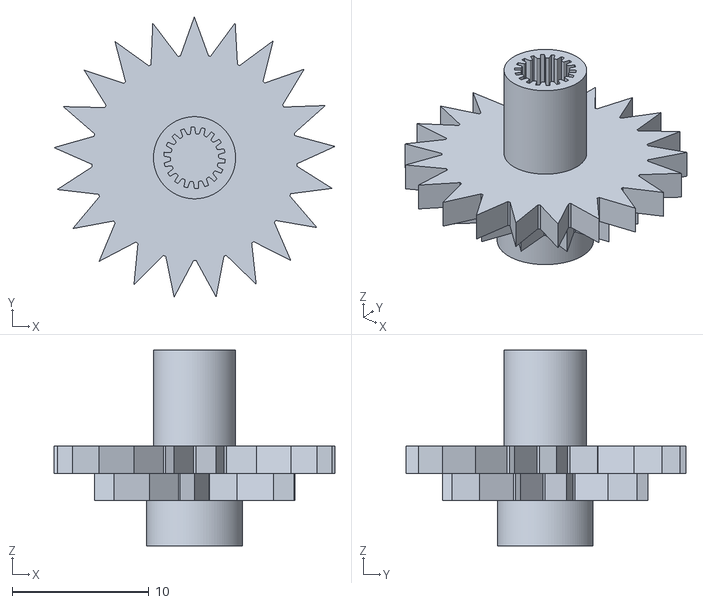
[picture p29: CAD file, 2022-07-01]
Robotic-Arm/Models/Gear1.stl
20.5 x 20.5 x 14.3

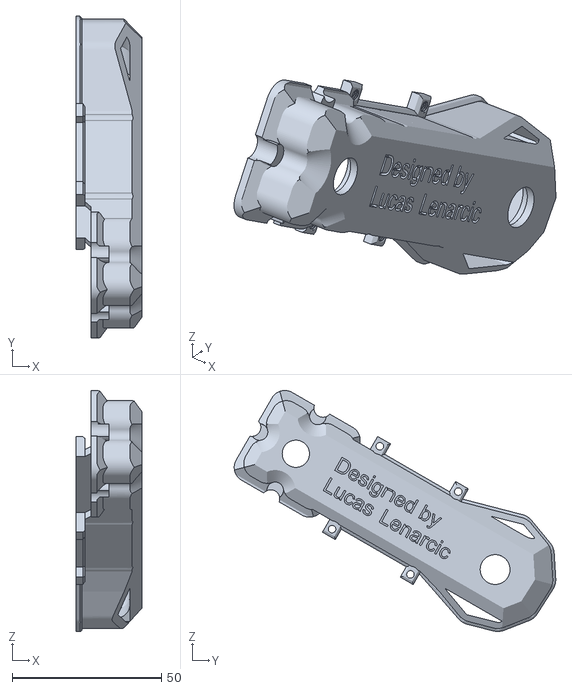
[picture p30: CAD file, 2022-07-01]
Robotic-Arm/Models/Cover.stl
22.0 x 107.9 x 80.8

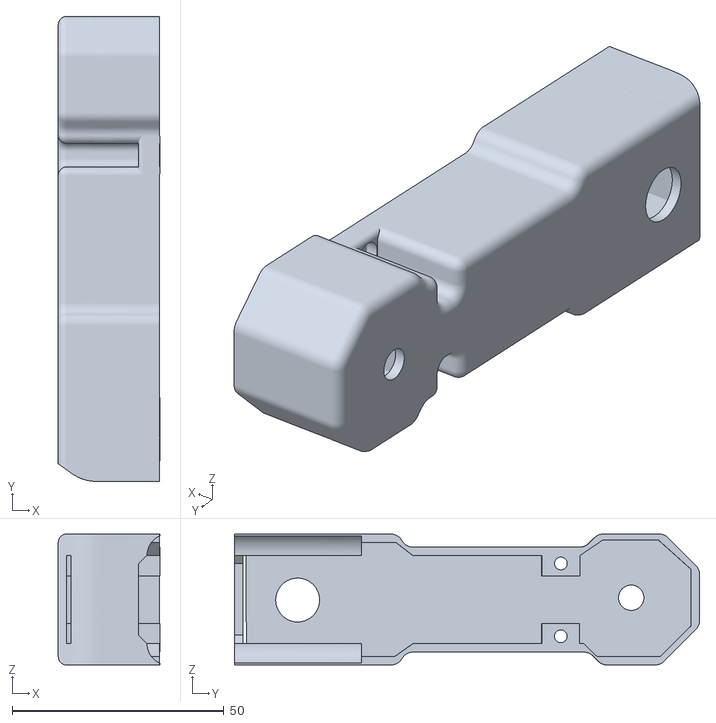
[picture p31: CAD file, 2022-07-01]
Robotic-Arm/Models/Arm4_Cover.stl
24.0 x 110.0 x 31.0

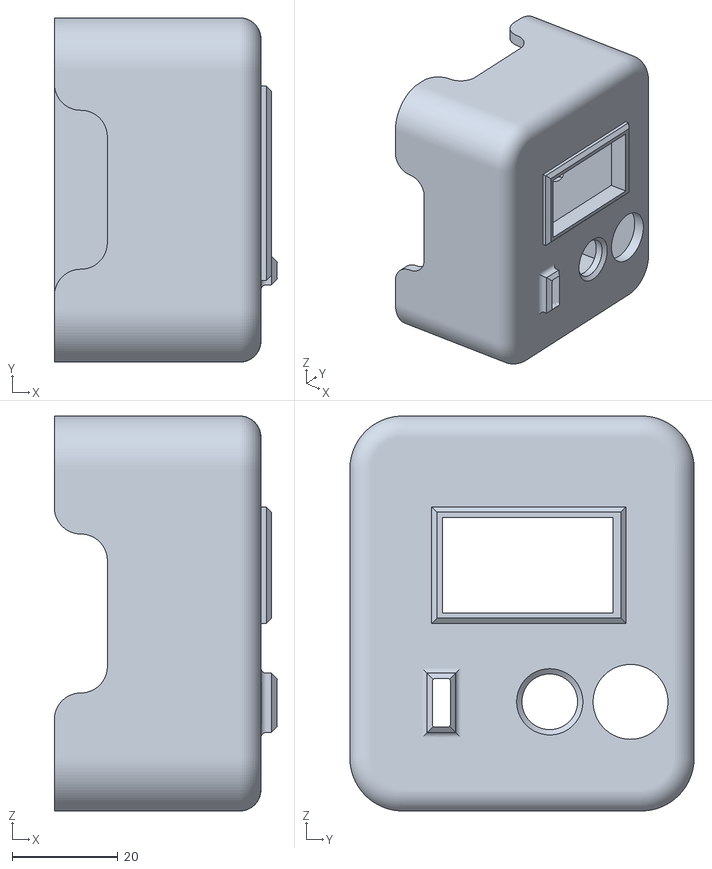
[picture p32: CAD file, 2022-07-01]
Robotic-Arm/Models/Front.stl
42.1 x 65.0 x 74.6

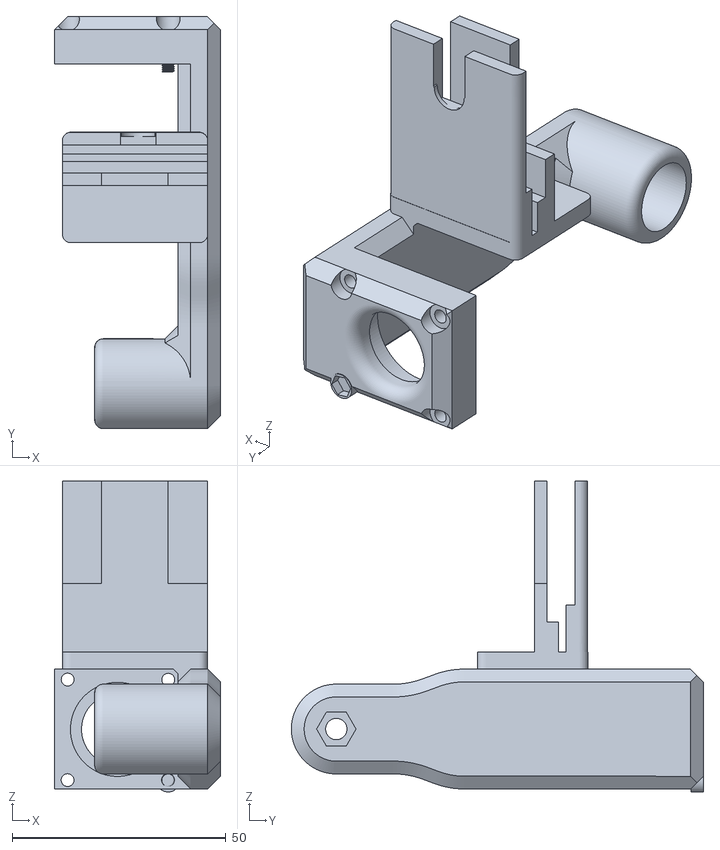
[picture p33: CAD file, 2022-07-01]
Robotic-Arm/Models/Arm5.stl
38.9 x 96.5 x 72.8

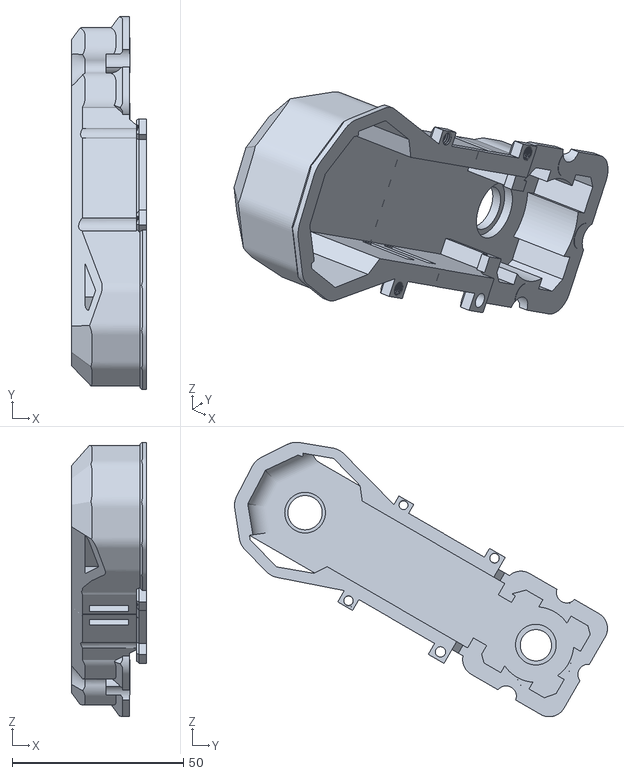
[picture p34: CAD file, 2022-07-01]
Robotic-Arm/Models/Cover2.stl
22.0 x 108.8 x 80.1

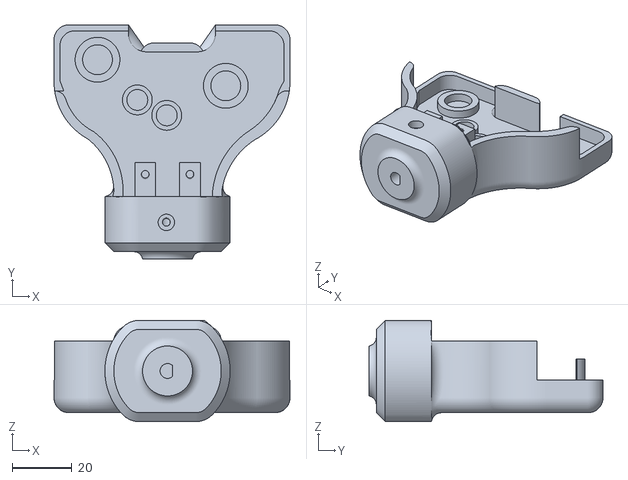
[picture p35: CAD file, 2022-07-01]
Robotic-Arm/Models/eoat_tool_base.stl
79.1 x 78.5 x 34.0

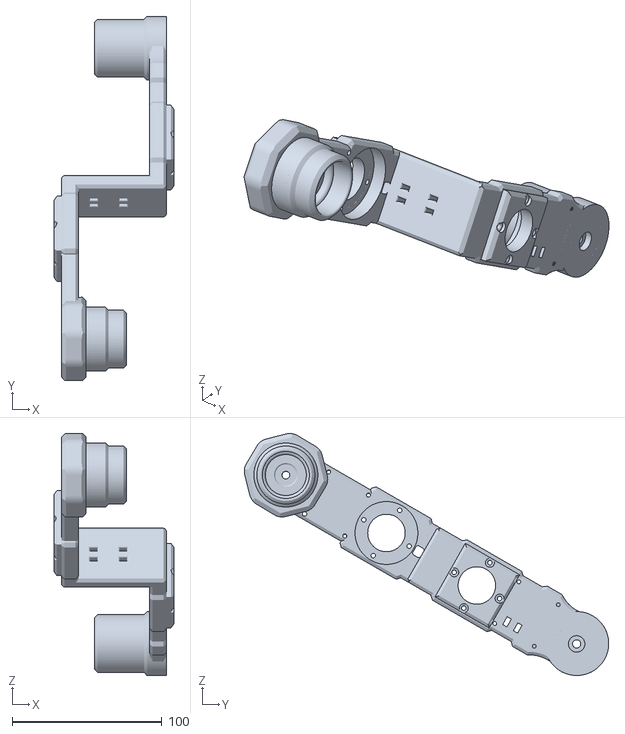
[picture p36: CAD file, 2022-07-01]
Robotic-Arm/Models/Arm2.stl
80.1 x 243.1 x 161.5

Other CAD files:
Robotic-Arm/Models/eoat_tool_arm2.stl
Robotic-Arm/Models/eoat_tool_arm1.stl
Robotic-Arm/Models/Motor_Base_2.stl
Robotic-Arm/Models/Motor_Base.stl
Robotic-Arm/Components/11HS20-0674S-PG51.f3d
Robotic-Arm/Components/17HS15-1684S-HG100.f3z
Robotic-Arm/Components/17HS4401 .f3d
Robotic-Arm/Components/LED-Ring.f3d
Robotic-Arm/Components/MainPCB.f3z
Robotic-Arm/Components/SteppperControllerNema11.f3d
Robotic-Arm/Components/SteppperControllerNema17.f3d
Robotic-Arm/Models/11HS20-0674S-PG51 v3.stl
Robotic-Arm/Models/Base-Cover.stl
Robotic-Arm/Models/Base-Motor.stl
Robotic-Arm/Models/Base.stl
Robotic-Arm/Models/Base_1_Laser_cutter.dwg
Robotic-Arm/Models/Base_2_Laser_cutter.dwg
Robotic-Arm/Models/Cover_Motors_2_Laser_cutter.dwg
Robotic-Arm/Models/Cover_Motors_Laser_cutter.dwg
Robotic-Arm/Models/LED_Ring_Laser_cutter.dwg

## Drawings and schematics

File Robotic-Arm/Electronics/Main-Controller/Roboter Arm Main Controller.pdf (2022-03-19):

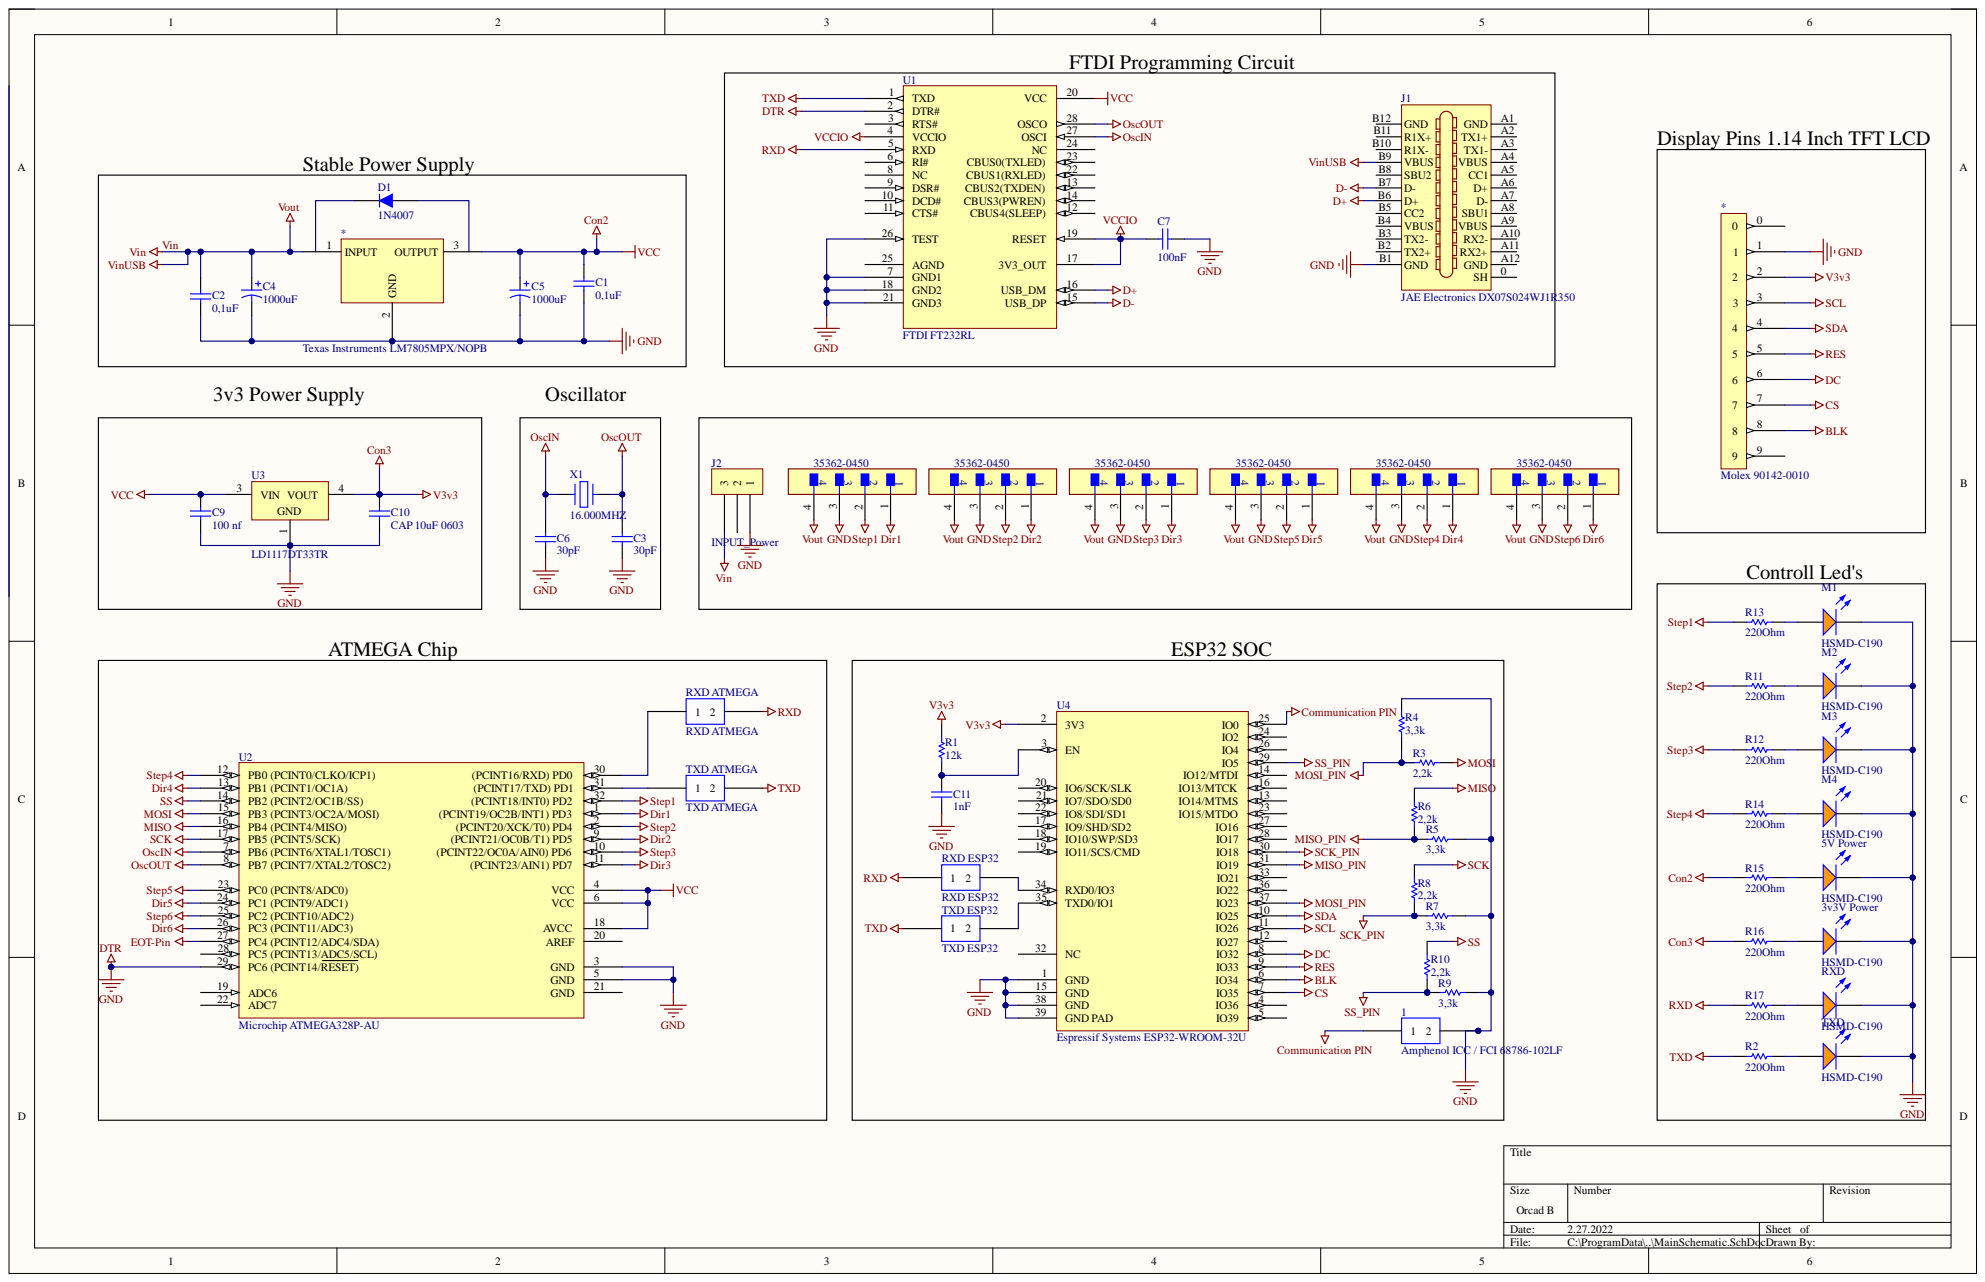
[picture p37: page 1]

GND 15

GND PAD 39

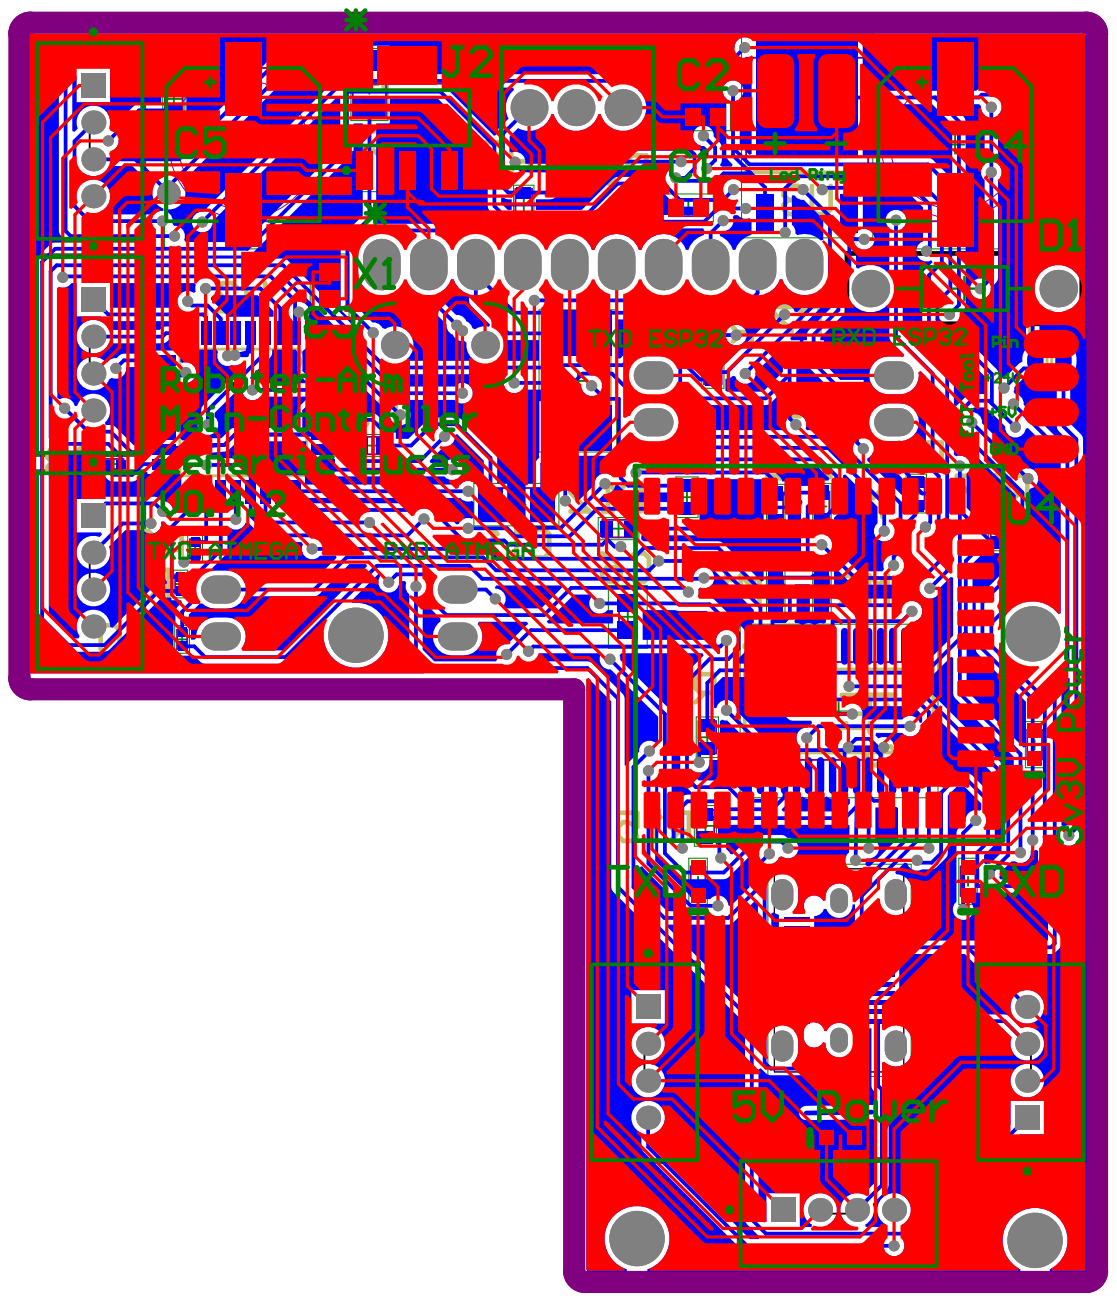
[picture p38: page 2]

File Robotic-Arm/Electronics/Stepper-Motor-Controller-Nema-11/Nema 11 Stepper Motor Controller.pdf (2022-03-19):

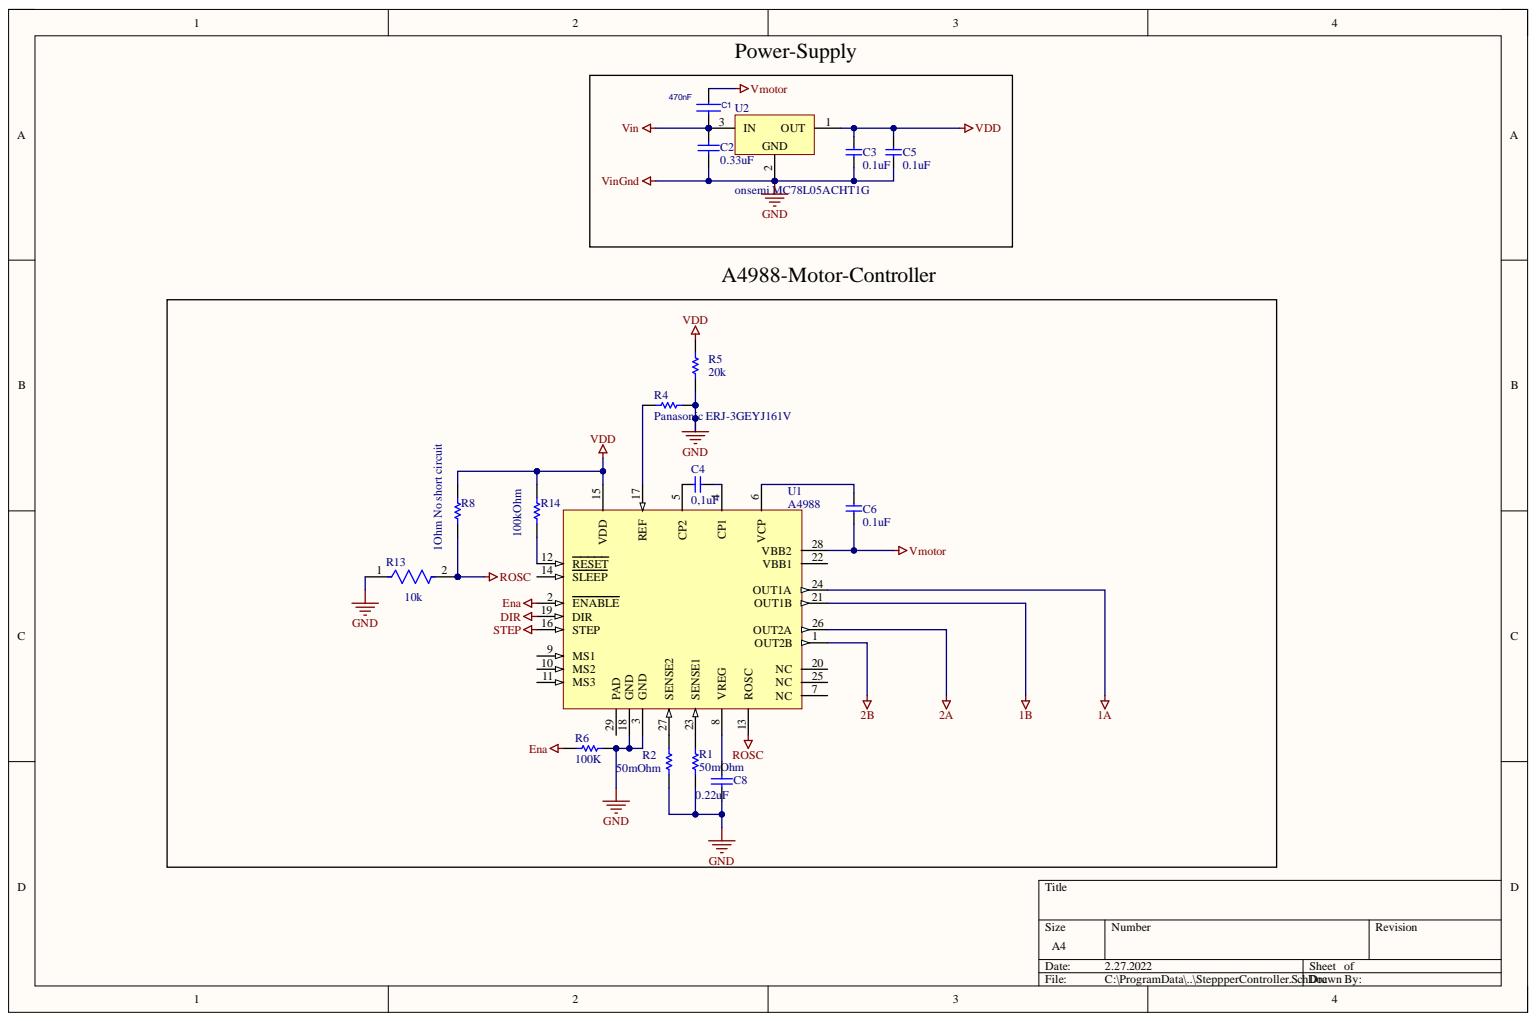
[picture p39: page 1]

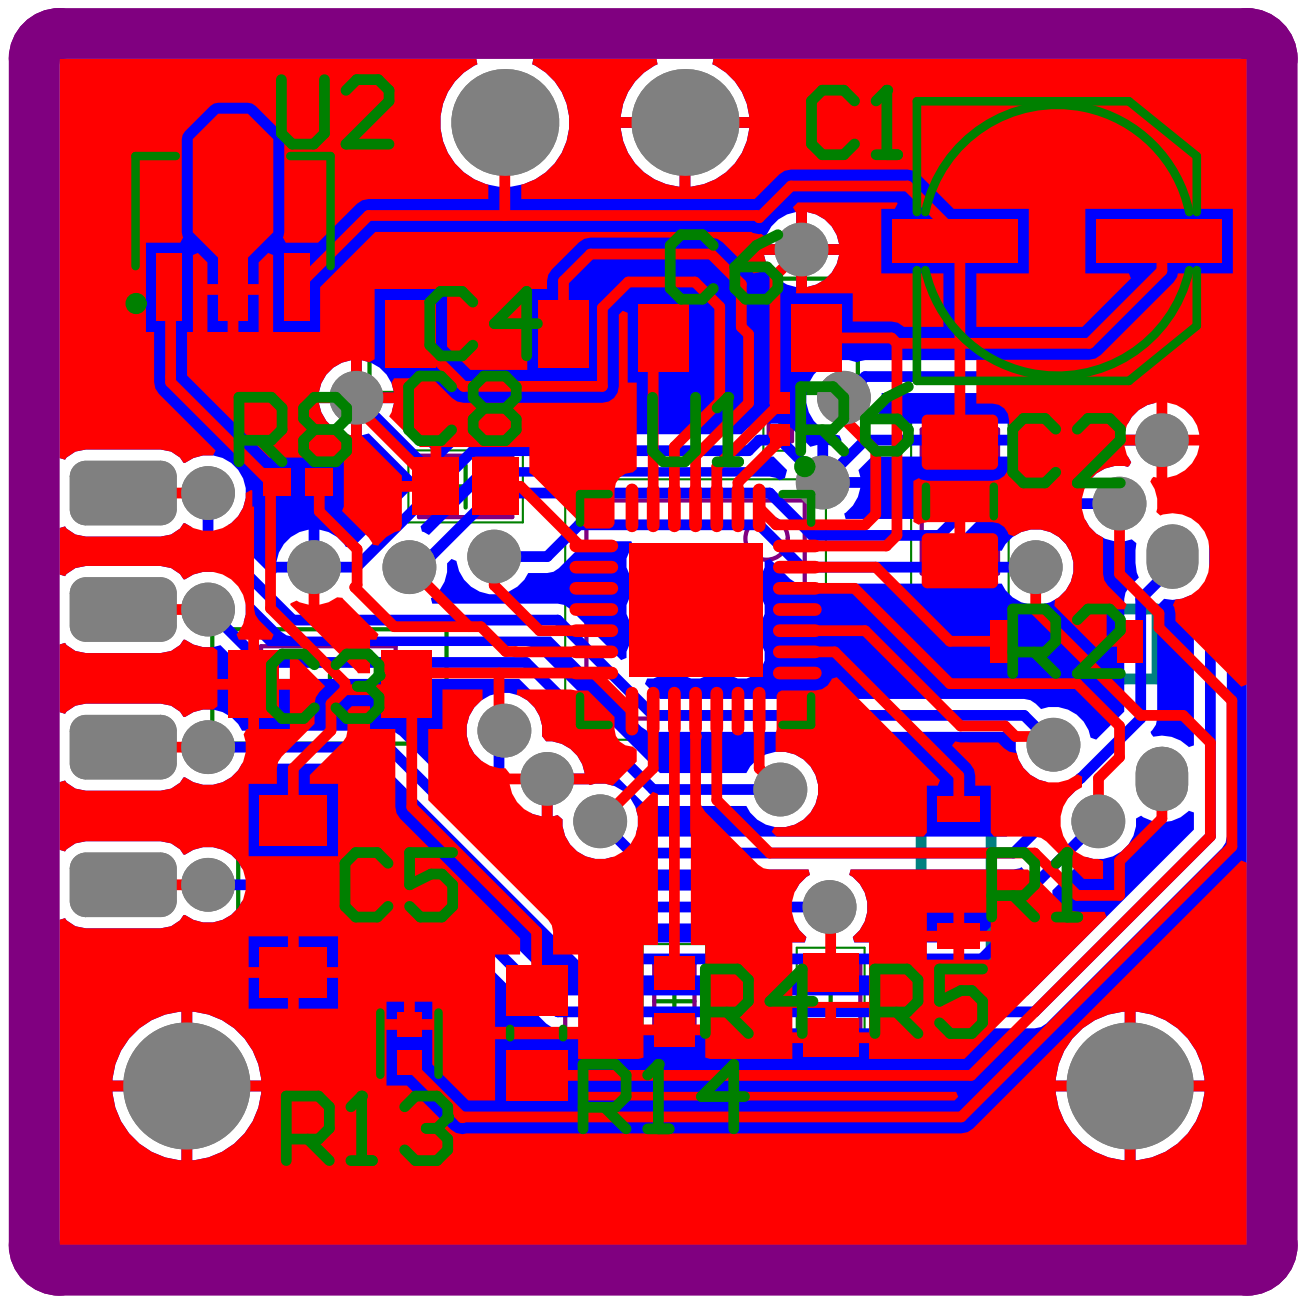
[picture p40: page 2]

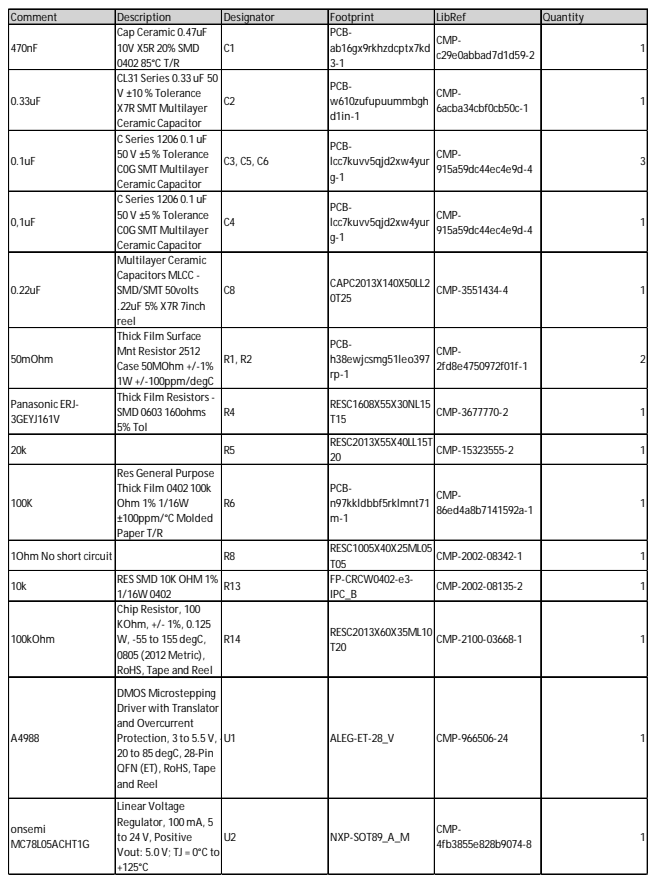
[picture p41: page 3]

Comment | Description | Designator | Footprint | LibRef | Quantity
470nF | Cap Ceramic 0.47uF 10V X5R 20% SMD 0402 85°C T/R | C1 | PCB-ab16gx9rkhzdcptx7kd 3-1 | CMP-c29e0abbad7d1d59-2 | 1

0.33uF | CL31 Series 0.33 uF 50 V ±10 % Tolerance X7R SMT Multilayer Ceramic Capacitor | C2 | PCB-w610zufupuummbgh d1in-1 | CMP-6acba34cbf0cb50c-1 | 1

0.1uF | C Series 1206 0.1 uF 50 V ±5 % Tolerance C0G SMT Multilayer Ceramic Capacitor | C3, C5, C6 | PCB-lcc7kuvv5qjd2xw4yur g-1 | CMP-915a59dc44ec4e9d-4 | 3

0,1uF | C Series 1206 0.1 uF 50 V ±5 % Tolerance C0G SMT Multilayer Ceramic Capacitor | C4 | PCB-lcc7kuvv5qjd2xw4yur g-1 | CMP-915a59dc44ec4e9d-4 | 1

0.22uF | Multilayer Ceramic Capacitors MLCC -SMD/SMT 50volts .22uF 5% X7R 7inch reel | C8 | CAPC2013X140X50LL2 0T25 | CMP-3551434-4 | 1

50mOhm | Thick Film Surface Mnt Resistor 2512 Case 50MOhm +/-1% 1W +/-100ppm/degC | R1, R2 | PCB-h38ewjcsmg51leo397 rp-1 | CMP-2fd8e4750972f01f-1 | 2

Panasonic ERJ-3GEYJ161V | Thick Film Resistors -SMD 0603 160ohms 5% Tol | R4 | RESC1608X55X30NL15 T15 | CMP-3677770-2 | 1

20k | | R5 | RESC2013X55X40LL15T 20 | CMP-15323555-2 | 1

100K | Res General Purpose Thick Film 0402 100k Ohm 1% 1/16W ±100ppm/°C Molded Paper T/R | R6 | PCB-n97kkldbbf5rklmnt71 m-1 | CMP-86ed4a8b7141592a-1 | 1

1Ohm No short circuit | | R8 | RESC1005X40X25ML05 T05 | CMP-2002-08342-1 | 1

10k | RES SMD 10K OHM 1% 1/16W 0402 | R13 | FP-CRCW0402-e3-IPC_B | CMP-2002-08135-2 | 1

100kOhm | Chip Resistor, 100 KOhm, +/- 1%, 0.125 W, -55 to 155 degC, 0805 (2012 Metric), RoHS, Tape and Reel | R14 | RESC2013X60X35ML10 T20 | CMP-2100-03668-1 | 1

A4988 | DMOS Microstepping Driver with Translator and Overcurrent Protection, 3 to 5.5 V, -20 to 85 degC, 28-Pin QFN (ET), RoHS, Tape and Reel | U1 | ALEG-ET-28_V | CMP-966506-24 | 1

onsemi MC78L05ACHT1G | Linear Voltage Regulator, 100mA, 5 to 24 V, Positive Vout: 5.0 V; TJ = 0°C to +125°C | U2 | NXP-SOT89_A_M | CMP-4fb3855e828b9074-8 | 1

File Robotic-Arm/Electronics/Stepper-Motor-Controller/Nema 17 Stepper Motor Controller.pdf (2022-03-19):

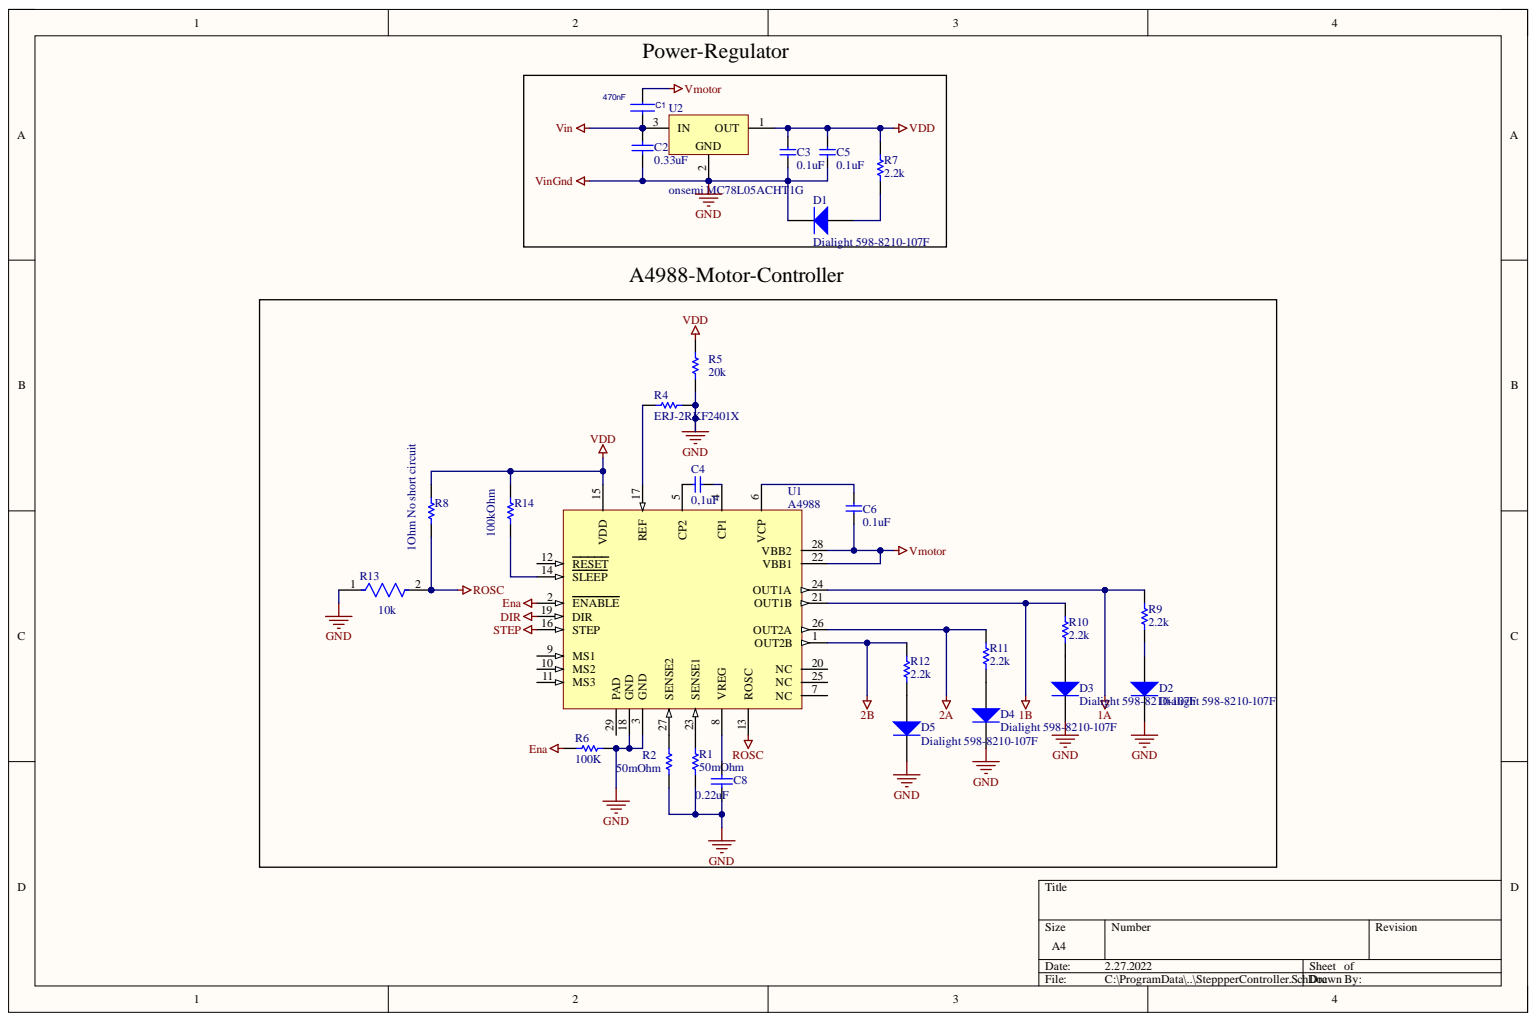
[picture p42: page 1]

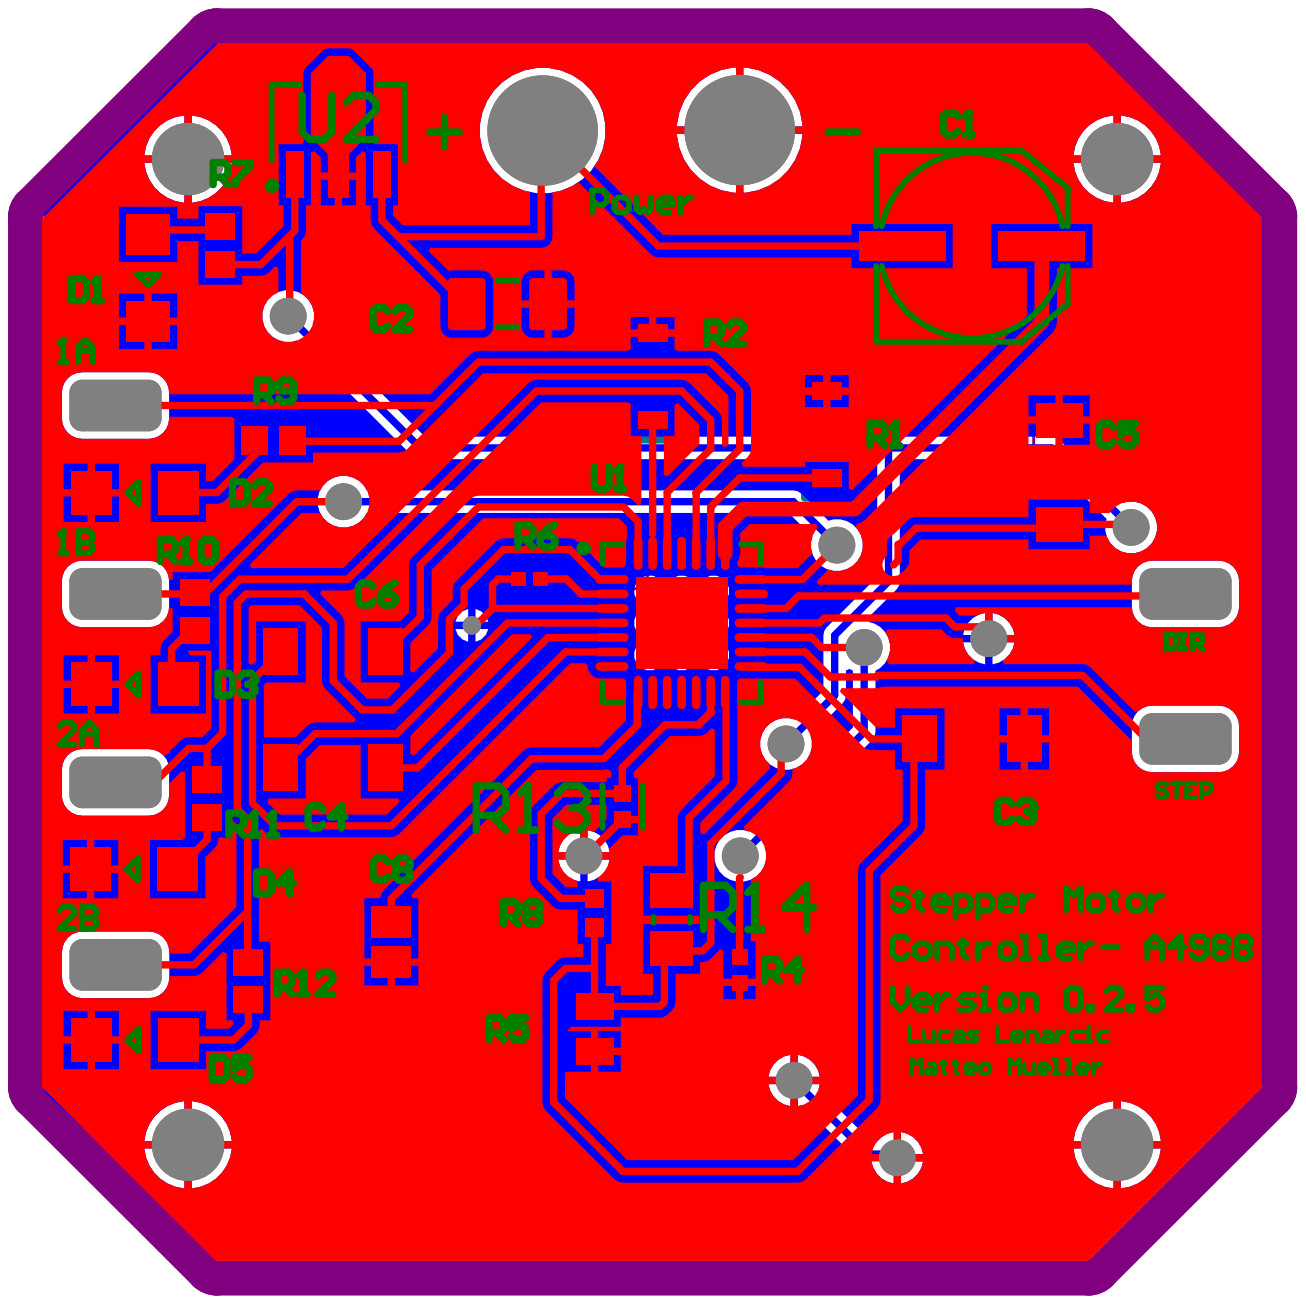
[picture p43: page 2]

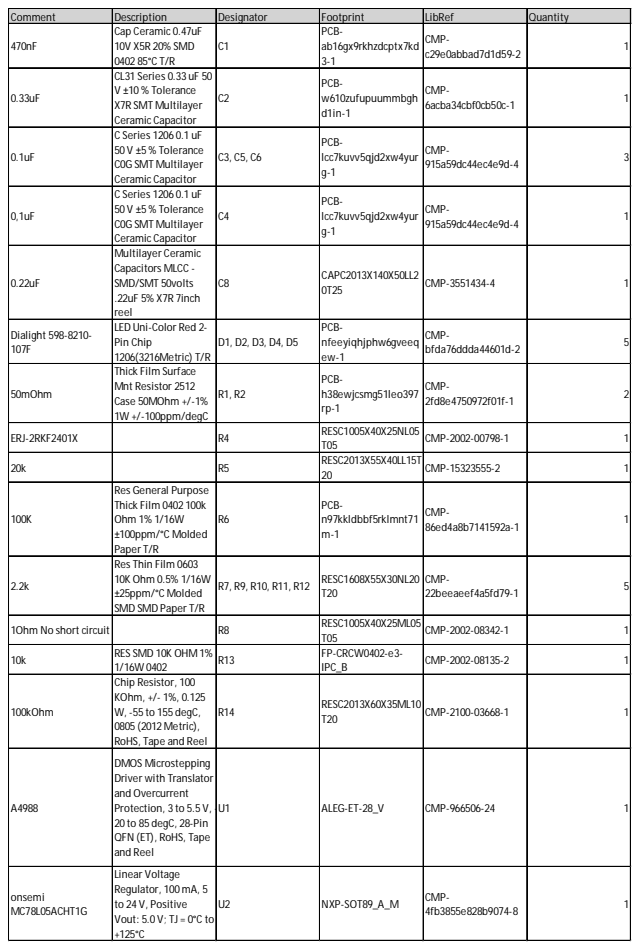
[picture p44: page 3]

Comment | Description | Designator | Footprint | LibRef | Quantity
470nF | Cap Ceramic 0.47uF 10V X5R 20% SMD 0402 85°C T/R | C1 | PCB-ab16gx9rkhzdcptx7kd 3-1 | CMP-c29e0abbad7d1d59-2 | 1

0.33uF | CL31 Series 0.33 uF 50 V ±10 % Tolerance X7R SMT Multilayer Ceramic Capacitor | C2 | PCB-w610zufupuummbgh d1in-1 | CMP-6acba34cbf0cb50c-1 | 1

0.1uF | C Series 1206 0.1 uF 50 V ±5 % Tolerance C0G SMT Multilayer Ceramic Capacitor | C3, C5, C6 | PCB-lcc7kuvv5qjd2xw4yur g-1 | CMP-915a59dc44ec4e9d-4 | 3

0,1uF | C Series 1206 0.1 uF 50 V ±5 % Tolerance C0G SMT Multilayer Ceramic Capacitor | C4 | PCB-lcc7kuvv5qjd2xw4yur g-1 | CMP-915a59dc44ec4e9d-4 | 1

0.22uF | Multilayer Ceramic Capacitors MLCC -SMD/SMT 50volts .22uF 5% X7R 7inch reel | C8 | CAPC2013X140X50LL2 0T25 | CMP-3551434-4 | 1

Dialight 598-8210-107F | LED Uni-Color Red 2-Pin Chip 1206(3216Metric) T/R | D1, D2, D3, D4, D5 | PCB-nfeeyiqhjphw6gveeq ew-1 | CMP-bfda76ddda44601d-2 | 5

50mOhm | Thick Film Surface Mnt Resistor 2512 Case 50MOhm +/-1% 1W +/-100ppm/degC | R1, R2 | PCB-h38ewjcsmg51leo397 rp-1 | CMP-2fd8e4750972f01f-1 | 2

ERJ-2RKF2401X | | R4 | RESC1005X40X25NL05 T05 | CMP-2002-00798-1 | 1

20k | | R5 | RESC2013X55X40LL15T 20 | CMP-15323555-2 | 1

100K | Res General Purpose Thick Film 0402 100k Ohm 1% 1/16W ±100ppm/°C Molded Paper T/R | R6 | PCB-n97kkldbbf5rklmnt71 m-1 | CMP-86ed4a8b7141592a-1 | 1

2.2k | Res Thin Film 0603 10K Ohm 0.5% 1/16W ±25ppm/°C Molded SMD SMD Paper T/R | R7, R9, R10, R11, R12 | RESC1608X55X30NL20 T20 | CMP-22beeaeef4a5fd79-1 | 5

1Ohm No short circuit | | R8 | RESC1005X40X25ML05 T05 | CMP-2002-08342-1 | 1

10k | RES SMD 10K OHM 1% 1/16W 0402 | R13 | FP-CRCW0402-e3-IPC_B | CMP-2002-08135-2 | 1

100kOhm | Chip Resistor, 100 KOhm, +/- 1%, 0.125 W, -55 to 155 degC, 0805 (2012 Metric), RoHS, Tape and Reel | R14 | RESC2013X60X35ML10 T20 | CMP-2100-03668-1 | 1

A4988 | DMOS Microstepping Driver with Translator and Overcurrent Protection, 3 to 5.5 V, -20 to 85 degC, 28-Pin QFN (ET), RoHS, Tape and Reel | U1 | ALEG-ET-28_V | CMP-966506-24 | 1

onsemi MC78L05ACHT1G | Linear Voltage Regulator, 100mA, 5 to 24 V, Positive Vout: 5.0 V; TJ = 0°C to +125°C | U2 | NXP-SOT89_A_M | CMP-4fb3855e828b9074-8 | 1

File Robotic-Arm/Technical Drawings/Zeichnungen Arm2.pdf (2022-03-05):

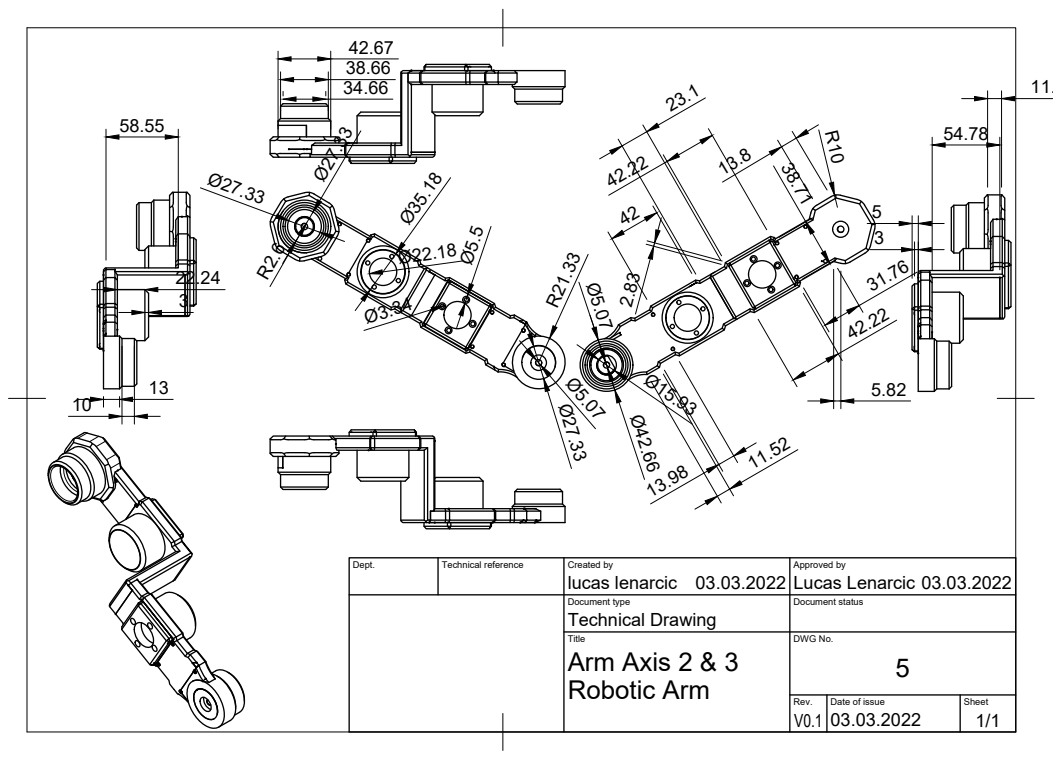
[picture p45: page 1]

Dept. | Technical reference | Created by lucas lenarcic 03.03.2022 | Approved by Lucas Lenarcic 03.03.2022

Document type Technical Drawing | Document status

Title Arm Axis 2 & 3 Robotic Arm | DWG No. 5

Rev. V0.1 | Date of issue 03.03.2022 | Sheet 1/1

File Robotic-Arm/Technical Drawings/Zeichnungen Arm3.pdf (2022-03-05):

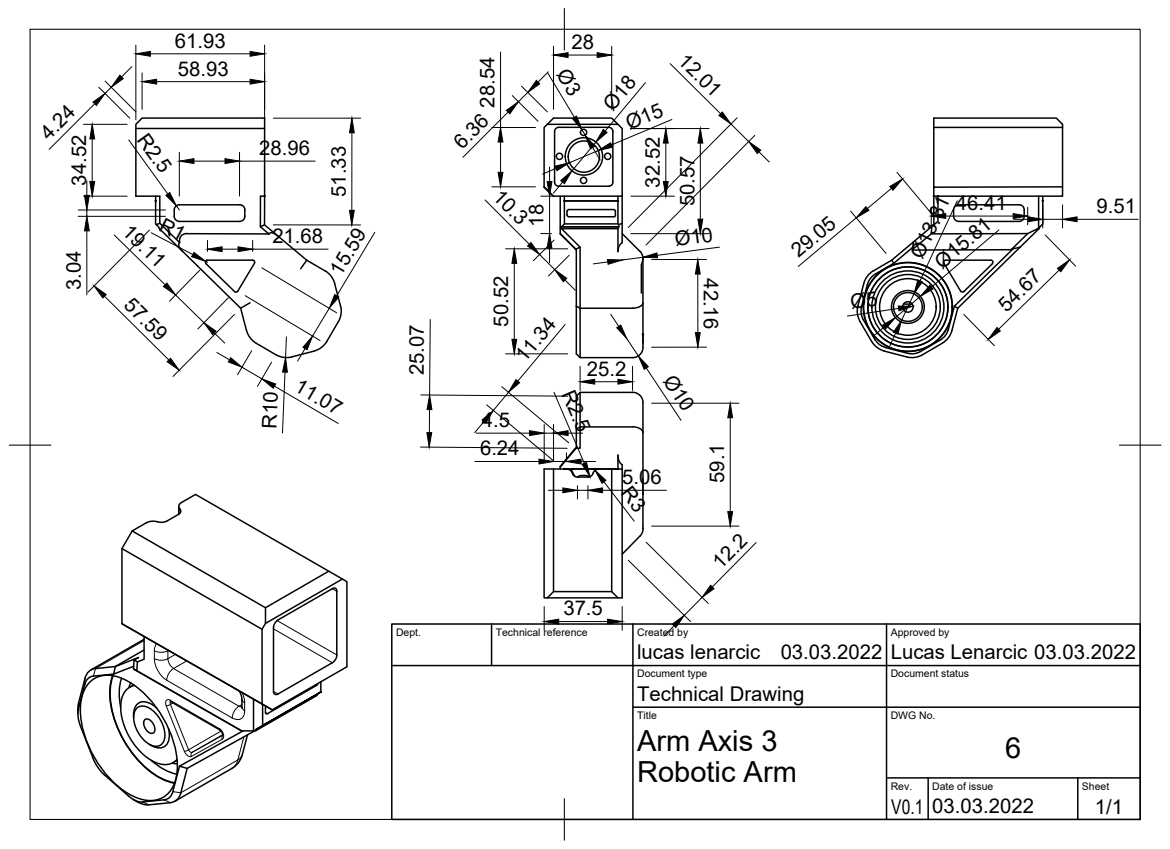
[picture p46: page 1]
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

Document type Technical Drawing | Document status

Title Arm Axis 3 Robotic Arm | DWG No. 6

Rev. V0.1 | Date of issue 03.03.2022 | Sheet 1/1

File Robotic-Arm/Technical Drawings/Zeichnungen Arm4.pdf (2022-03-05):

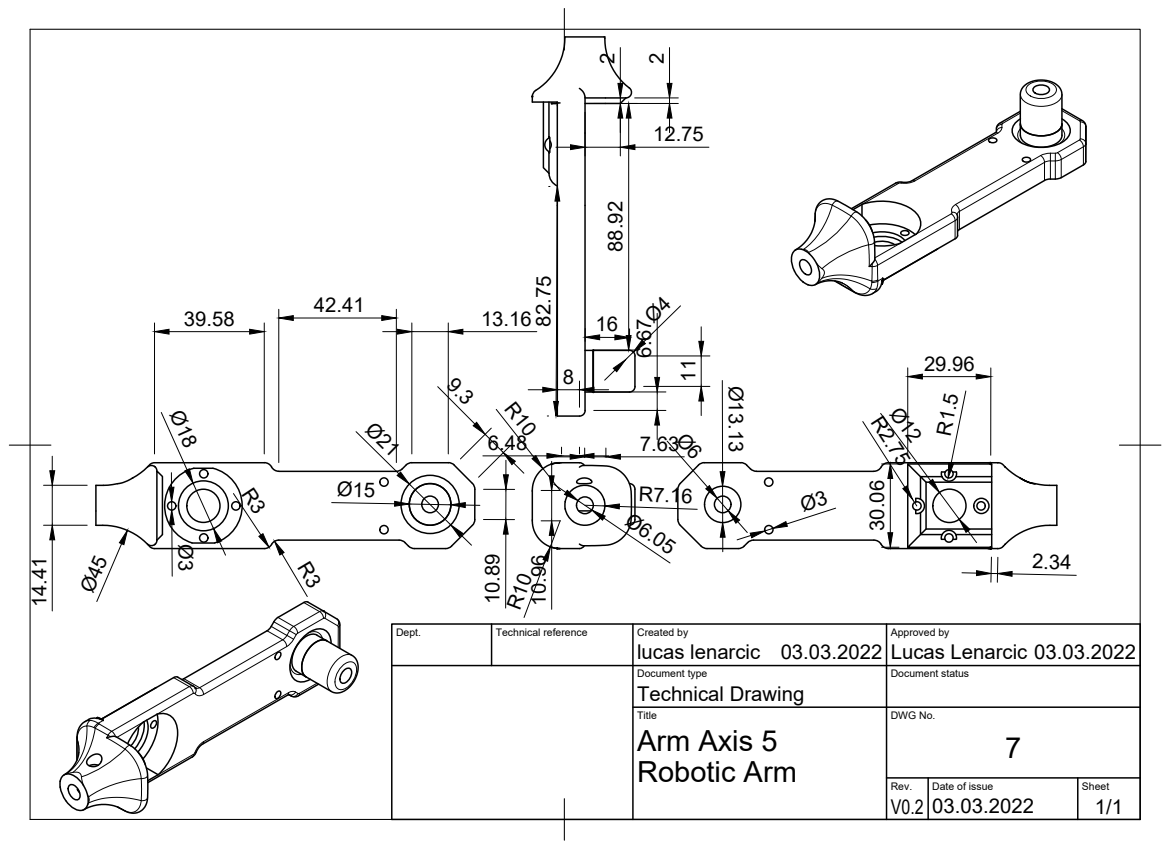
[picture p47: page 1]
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

Document type Technical Drawing | Document status

Title Arm Axis 5 Robotic Arm | DWG No. 7

Rev. V0.2 | Date of issue 03.03.2022 | Sheet 1/1

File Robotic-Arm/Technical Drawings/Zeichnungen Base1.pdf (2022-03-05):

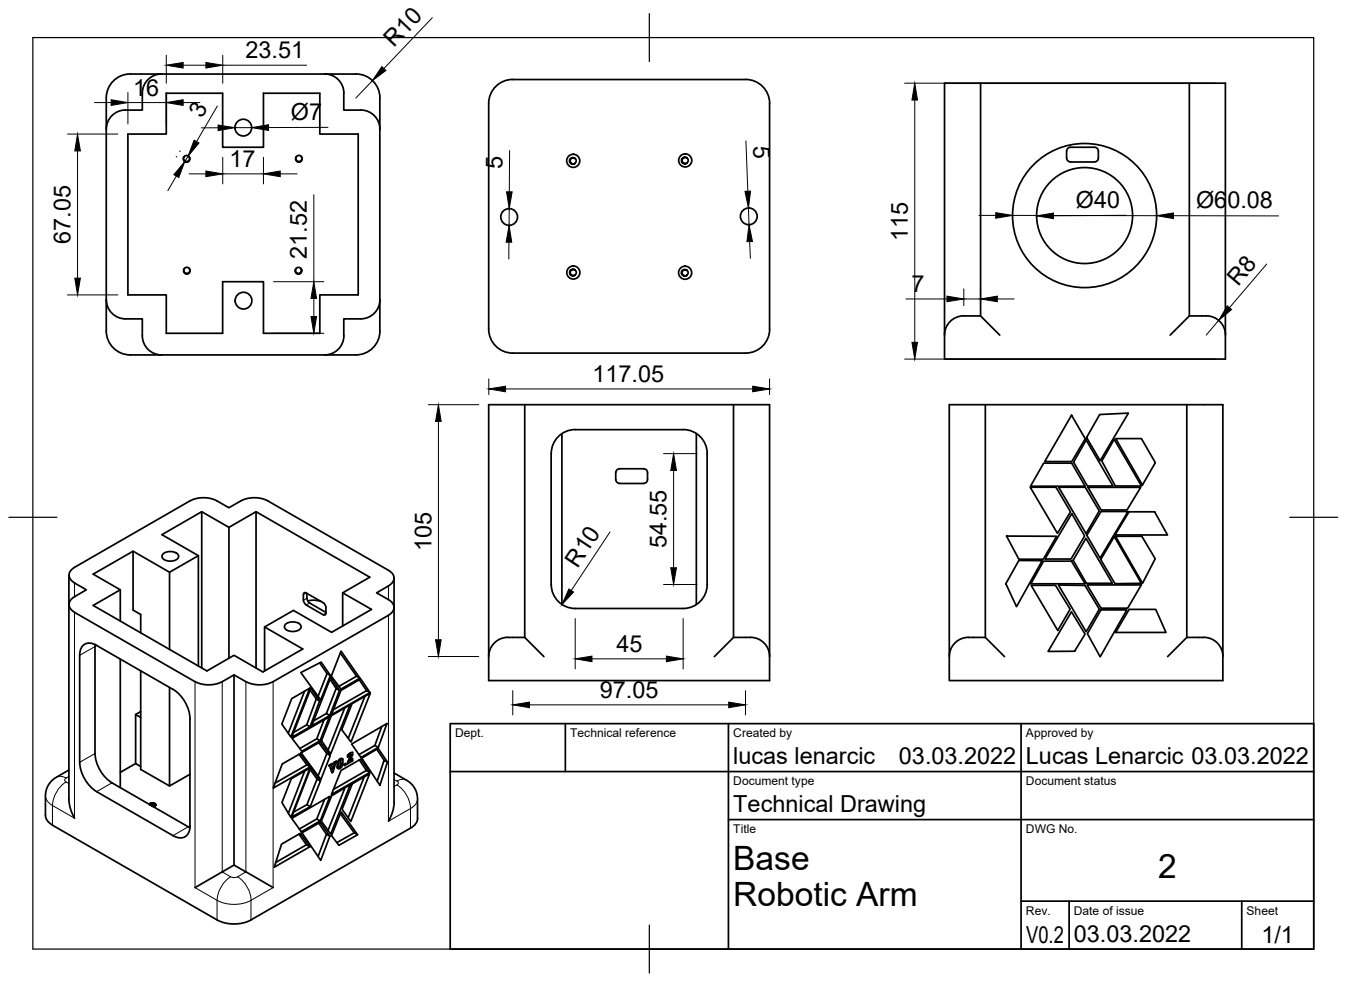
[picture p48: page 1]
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

Document type Technical Drawing | Document status

Title Base Robotic Arm | DWG No. 2

Rev. V0.2 | Date of issue 03.03.2022 | Sheet 1/1

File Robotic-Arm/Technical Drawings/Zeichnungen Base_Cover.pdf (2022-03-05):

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

Document type Technical Drawing | Document status

Title Base-Cover Robotic Arm | DWG No. 3

Rev. V0.2 | Date of issue 03.03.2022 | Sheet 1/1

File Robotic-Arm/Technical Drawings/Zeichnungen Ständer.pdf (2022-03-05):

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

Document type Technical Drawing | Document status

Title Base Stand Robotic Arm | DWG No. 1

Rev. V0.2 | Date of issue 03.03.2022 | Sheet 1/1

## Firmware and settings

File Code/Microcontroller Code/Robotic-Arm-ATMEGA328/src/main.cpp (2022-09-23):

#include <Arduino.h>
#include <avr/io.h>
#include <AccelStepper.h>
#include "Main_Header.h"
#include <SPI.h>
#include <EEPROM.h>


#define STATE_LOCATION 513
#define EEPROM_BUFFER 514
#define BUFFER_LENGTH 121
#define motor_length 7
#define motor_arr 20

// O -- STOP
// H -- HOLD
// S -- SAVE
// R -- Read
// D -- Drive
// E -- END
// c -- ATMEGA Check
// A -- response coordinates 
// l -- löschen vom eeprom (test feature)
// f -- speed check


char buf[50];
volatile byte pos;
volatile boolean senden;

int motor_values[motor_length];
int arr_motor_value[motor_arr][motor_length];
String motor_values_return[motor_length];
bool drive_check = false;

int arr_counter = 0;
String conv = "";
int counter = 0;
int last_stop = 0;
bool hold = false;

int tempPin = 0;      
int printPin = 2;     
int erasePin = 4;    
int address = 0;   
bool testmode = true; 

String input_terminal;
bool test_inter = false;
 

#define step1 2
#define step2 4
#define step3 6
#define step4 8
#define step5 14
#define step6 16

#define dir1 3
#define dir2 5
#define dir3 7
#define dir4 9
#define dir5 15
#define dir6 17

Motor motor1(step1, dir1, 1);
Motor motor2(step2, dir2, 1);
Motor motor3(step3, dir3, 1);
Motor motor4(step4, dir4, 1);
Motor motor5(step5, dir5, 1);
Motor motor6(step6, dir6, 1);


void setup() {
  Serial.begin(9600);
  Serial.println("Starting setup(): ");

  SPCR |= bit(SPE);

  pinMode(MISO, OUTPUT);

  pos = 0;
  senden = false;

  SPI.attachInterrupt();

  DDRD |= 0b11111100;
  DDRB |= 0b00000011;
  DDRC |= 0b00011111;
   Serial.println("Starting loop(): ");
   Serial.println("Test Features:  ");
   Serial.println("");
}

void driveMotors() {
  Serial.println("Starting first row of coordinates: ");
  do{
    if (buf[0] != 'H' && buf[0] != 'O') {
      motor1.setmoveto(arr_motor_value[last_stop][0]);
      Serial.print(arr_motor_value[last_stop][0]);
      Serial.print(", ");
      motor2.setmoveto(arr_motor_value[last_stop][1]);
      Serial.print(arr_motor_value[last_stop][1]);
      Serial.print(", ");
      motor3.setmoveto(arr_motor_value[last_stop][2]);
      Serial.print(arr_motor_value[last_stop][2]);
      Serial.print(", ");
      motor4.setmoveto(arr_motor_value[last_stop][3]);
      Serial.print(arr_motor_value[last_stop][3]);
      Serial.print(", ");
      motor5.setmoveto(arr_motor_value[last_stop][4]);
      Serial.print(arr_motor_value[last_stop][4]);
      Serial.print(", ");
      motor6.setmoveto(arr_motor_value[last_stop][5]);
      Serial.print(arr_motor_value[last_stop][5]);
      Serial.print(", ");
      driveMotor(motor1, motor2, motor3, motor4, motor5, motor6);
      Serial.println();

      motor_values_return[0] = arr_motor_value[last_stop][motor_values[0]];
      motor_values_return[1] = arr_motor_value[last_stop][motor_values[1]];
      motor_values_return[2] = arr_motor_value[last_stop][motor_values[2]];
      motor_values_return[3] = arr_motor_value[last_stop][motor_values[3]];
      motor_values_return[4] = arr_motor_value[last_stop][motor_values[4]];
      motor_values_return[5] = arr_motor_value[last_stop][motor_values[5]];



    } else if (buf[0] != 'O' || input_terminal == "Stop") {
      last_stop == arr_counter;
      Serial.println("Stopping Motors");
    } else if (buf[0] != 'H' || input_terminal == "Hold") {
      hold = true;
      Serial.println("Holding Motors");
    }

    last_stop++;

   if(hold == false ){
     drive_check = true;
   }else if( last_stop < arr_counter){
     drive_check = true;
   }
    
  }while(drive_check == false);

  drive_check = false;
  last_stop = 0;
}

void ReadInput() {
  if (arr_counter == motor_arr-1) {
    arr_counter = 0;
  }
  for (int i = 0; i < pos; i++) {
    if (buf[i] != ',') {
      conv += buf[i];
      Serial.println("Reading Input Char: " + conv);
    } else {
      motor_values[counter] = conv.toInt();      
      arr_motor_value[arr_counter][counter] =  conv.toInt();  
      Serial.println("Input Char to int: " + conv.toInt());
      counter++;
    }
  }

  arr_counter++;
}

void SaveCommands() {
  for(int i = 0; i < motor_arr; i++){
    for(int j = 0; j < motor_length; j++){
      EEPROM.write(address, arr_motor_value[i][motor_values[j]]);         
      Serial.print("Motor value stored at address ");
      Serial.println(address);
      address++;   

      if(address == EEPROM.length()) 
      {
       address = 0;              
      } 
    }
  } 
}

void clearEEPROM()
{
  for (int i = 0 ; i < EEPROM.length() ; i++) {
    if(EEPROM.read(i) != 0)                     
    {
      EEPROM.write(i, 0);                      
    }
  }
  Serial.println("EEPROM erased");
  address = 0;                                  
}

void testProgramm(){
      if(input_terminal == "Stop Test"){
			Serial.println("Ending Serial Communication");
		  testmode = false;
		}

       
    if(input_terminal == "Test") {
       Serial.println("Giving Motor Array Values!");
       arr_motor_value[0][0] = 180;
       Serial.print(arr_motor_value[0][0]);
       Serial.print(", ");
       arr_motor_value[0][1] = 90;
       Serial.print(arr_motor_value[0][1]);
       Serial.print(", ");
       arr_motor_value[0][2] = 45;
       Serial.print(arr_motor_value[0][2]);
       Serial.print(", ");
       arr_motor_value[0][3] = 30;
       Serial.print(arr_motor_value[0][3]);
       Serial.print(", ");
       arr_motor_value[0][4] = 10;
       Serial.print(arr_motor_value[0][4]);
       Serial.print(", ");
       arr_motor_value[0][5] = 340;
       Serial.print(arr_motor_value[0][5]);
       arr_counter=1;
       Serial.println("");
       Serial.println("");
    }

    if (input_terminal == "Read") {
       Serial.println("Starting to Read Input Data...");
      ReadInput();
      Serial.println("Finished Read Input Data!");
      Serial.println("");
      Serial.println("");
    }

    if (input_terminal == "Save") {
      Serial.println("Starting to Save Commands to EEPROM...");
      SaveCommands();
      Serial.println("Finished Save Commands to EEPROM!");
      Serial.println("");
      Serial.println("");
    }

    if (input_terminal == "Drive") {
       Serial.println("Starting to Drive Motors...");
      driveMotors();
      Serial.println("Finished Driving Motors!");
      Serial.println("");
      Serial.println("");
    }

    if (input_terminal == "Delete") {
      Serial.println("Deleting EEPROM...");
      clearEEPROM();
      Serial.println("Finished Deleting EEPROM!");
      Serial.println("");
      Serial.println("");
    }
}

void mainProgramm(){

  if (buf[pos] == 'E') {

    if (buf[0] == 'R') {
       Serial.println("Starting to Read Input Data...");
      ReadInput();
      Serial.println("Finished Read Input Data!");
      Serial.println("");
    }

    if (buf[0] == 'S') {
      Serial.println("Starting to Save Commands to EEPROM...");
      SaveCommands();
      Serial.println("Finished Save Commands to EEPROM!");
      Serial.println("");
    }

    if (buf[0] == 'D') {
       Serial.println("Starting to Drive Motors...");
      driveMotors();
      Serial.println("Finished Driving Motors!");
      Serial.println("");
    }

    if (buf[0] == 'l') {
      Serial.println("Deleting EEPROM...");
      clearEEPROM();
      Serial.println("Finished Deleting EEPROM!");
      Serial.println("");
    }   
  }
}

void loop() {


  if(Serial.available() && testmode == true){
        input_terminal = Serial.readStringUntil('\n');
        testProgramm();
  }

  if(!Serial.available()){
     testmode == false;
  }

  mainProgramm();
}



ISR(SPI_STC_vect) {
  Serial.println("Incoming input from ESP32...");
  byte c = SPDR;
  for (size_t i = 0; i < 50; i++)
  {
    buf[i] = ' ';
  }
  

  if (pos < sizeof buf) {
    buf[pos++] = c;
  }

  if (buf[0] == 'C') {
     Serial.println("Sending Check back...");
    SPI.transfer(true);
  }

  if (buf[0] == 'A') {
    Serial.println("Sending Motor Values back...");
    for (int i = 0; i < motor_length; i++) {
      for (int j = 0; j < sizeof(motor_values_return[i]); j++) {
        SPI.transfer(motor_values_return[i].charAt(j));
      }
    }
  }
  

   if (buf[0] == 'f') {
     Serial.println("Sending speed back...");
     SPI.transfer(get_speed());
  }
}

/*

// Define stepper motor connections and motor interface type. Motor interface type must be set to 1 when using a driver:
#define dirPin 3
#define stepPin 2
#define motorInterfaceType 1

// Create a new instance of the AccelStepper class:
AccelStepper stepper = AccelStepper(motorInterfaceType, stepPin, dirPin);

void setup() {
  // Set the maximum speed in steps per second:
  stepper.setMaxSpeed(6000);
}

void loop() {
  // Set the speed in steps per second:
  stepper.setSpeed(400);
  // Step the motor with a constant speed as set by setSpeed():
  stepper.runSpeed();
}*/

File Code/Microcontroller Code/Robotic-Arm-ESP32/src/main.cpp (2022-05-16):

#include <Arduino.h>
#include <TFT_eSPI.h>
#include "header.h"
#include <SPI.h>
#include <string>
   

extern int web;
extern int display;
bool mc = true;
String input_terminal;
String Website_input = "";
int arr_motor_value[20][6];
String atmega_input = "";

#define PIN_SCK 18
#define PIN_MOSI  23
#define PIN_MISO  19
#define RESET 33

bool testmode = true; 
bool state_1 = false;
bool state_2 = false;

bool old_state_1 = false;
bool old_state_2 = false;

const int chipSelectPin = 5;
int test_counter_1 = 0;

//TFT_eSPI.h had to be edited 
//Bitmap Web and Power
const unsigned char bitmap [] PROGMEM = {
	// 'display, 240x135px
	0xff, 0xff, 0xff, 0xff, 0xff, 0xff, 0xff, 0xff, 0xff, 0xff, 0xff, 0xff, 0xff, 0xff, 0xff, 0xff, 
	0xff, 0xff, 0xff, 0xff, 0xff, 0xff, 0xff, 0xff, 0xff, 0xff, 0xff, 0xff, 0xff, 0xff, 0xff, 0xff, 
	0xff, 0xff, 0xff, 0xff, 0xff, 0xff, 0xff, 0xff, 0xff, 0xff, 0xff, 0xff, 0xff, 0xff, 0xff, 0xff, 
	0xff, 0xff, 0xff, 0xff, 0xff, 0xff, 0xff, 0xff, 0xff, 0xff, 0xff, 0xff, 0xff, 0xff, 0xff, 0xff, 
	0xff, 0xff, 0xff, 0xff, 0xff, 0xff, 0xff, 0xff, 0xff, 0xff, 0xff, 0xff, 0xff, 0xff, 0xff, 0xff, 
	0xff, 0xff, 0xff, 0xff, 0xff, 0xff, 0xff, 0xff, 0xff, 0xff, 0xff, 0xff, 0xff, 0xff, 0xff, 0xff, 
	0xff, 0xff, 0xff, 0xff, 0xff, 0xff, 0xff, 0xff, 0xff, 0xff, 0xff, 0xff, 0xff, 0xff, 0xff, 0xff, 
	0xff, 0xff, 0xff, 0xff, 0xff, 0xff, 0xff, 0xff, 0xff, 0xff, 0xff, 0xff, 0xff, 0xff, 0xff, 0xff, 
	0xff, 0xff, 0xff, 0xff, 0xff, 0xff, 0xff, 0xff, 0xff, 0xff, 0xff, 0xff, 0xff, 0xff, 0xff, 0xff, 
	0xff, 0xff, 0xff, 0xff, 0xff, 0xff, 0xff, 0xff, 0xff, 0xff, 0xff, 0xff, 0xff, 0xff, 0xff, 0xff, 
	0xff, 0xff, 0xff, 0xff, 0xff, 0xff, 0xff, 0xff, 0xff, 0xff, 0xff, 0xff, 0xff, 0xff, 0xff, 0xff, 
	0xff, 0xff, 0xff, 0xff, 0xff, 0xff, 0xff, 0xff, 0xff, 0xff, 0xff, 0xff, 0xff, 0xff, 0xff, 0xff, 
	0xff, 0xff, 0xff, 0xff, 0xff, 0xff, 0xff, 0xff, 0xff, 0xff, 0xff, 0xff, 0xff, 0xff, 0xff, 0xff, 
	0xff, 0xff, 0xff, 0xff, 0xff, 0xff, 0xff, 0xff, 0xff, 0xff, 0xff, 0xff, 0xff, 0xff, 0xff, 0xff, 
	0xff, 0xff, 0xff, 0xff, 0xff, 0xff, 0xff, 0xff, 0xff, 0xff, 0xff, 0xff, 0xff, 0xff, 0xff, 0xff, 
	0xff, 0xff, 0xff, 0xff, 0xff, 0xff, 0xff, 0xff, 0xff, 0xff, 0xff, 0xff, 0xff, 0xff, 0xff, 0xff, 
	0xff, 0xff, 0xff, 0xff, 0xff, 0xff, 0xff, 0xff, 0xff, 0xff, 0xff, 0xff, 0xff, 0xff, 0xff, 0xff, 
	0xff, 0xff, 0xff, 0xff, 0xff, 0xff, 0xff, 0xff, 0xff, 0xff, 0xff, 0xff, 0xff, 0xff, 0xff, 0xff, 
	0xff, 0xff, 0xff, 0xff, 0xff, 0xff, 0xff, 0xff, 0xff, 0xff, 0xff, 0xff, 0xff, 0xff, 0xff, 0xff, 
	0xff, 0xff, 0xff, 0xff, 0xff, 0xff, 0xff, 0xff, 0xff, 0xff, 0xff, 0xff, 0xff, 0xff, 0xff, 0xff, 
	0xff, 0xff, 0xff, 0xff, 0xff, 0xff, 0xff, 0xff, 0xff, 0xff, 0xff, 0xff, 0xff, 0xff, 0xff, 0xff, 
	0xff, 0xff, 0xff, 0xff, 0xff, 0xff, 0xff, 0xff, 0xff, 0xff, 0xff, 0xff, 0xff, 0xff, 0xff, 0xff, 
	0xff, 0xff, 0xff, 0xff, 0xff, 0xff, 0xff, 0xff, 0xff, 0xff, 0xff, 0xff, 0xff, 0xff, 0xff, 0xff, 
	0xff, 0xff, 0xff, 0xff, 0xff, 0xff, 0xff, 0xff, 0xff, 0xff, 0xff, 0xff, 0xff, 0xff, 0xff, 0xff, 
	0xff, 0xff, 0xff, 0xff, 0xff, 0xff, 0xff, 0xff, 0xff, 0xff, 0xff, 0xff, 0xff, 0xff, 0xff, 0xff, 
	0xff, 0xff, 0xff, 0xff, 0xff, 0xff, 0xff, 0xff, 0xff, 0xff, 0xff, 0xff, 0xff, 0xff, 0xff, 0xff, 
	0xff, 0xff, 0xff, 0xff, 0xff, 0xff, 0xff, 0xff, 0xff, 0xff, 0xff, 0xff, 0xff, 0xff, 0xff, 0xff, 
	0xff, 0xff, 0xff, 0xff, 0xff, 0xff, 0xff, 0xff, 0xff, 0xff, 0xff, 0xff, 0xff, 0xff, 0xff, 0xff, 
	0xff, 0xff, 0xff, 0xff, 0xff, 0xff, 0xff, 0xff, 0xff, 0xff, 0xff, 0xff, 0xff, 0xff, 0xff, 0xff, 
	0xff, 0xff, 0xff, 0xff, 0xff, 0xff, 0xff, 0xff, 0xff, 0xff, 0xff, 0xff, 0xff, 0xff, 0xff, 0xff, 
	0xff, 0xff, 0xff, 0xff, 0xff, 0xff, 0xff, 0xff, 0xff, 0xff, 0xff, 0xff, 0xff, 0xff, 0xff, 0xff, 
	0xff, 0xff, 0xff, 0xff, 0xff, 0xff, 0xff, 0xff, 0xff, 0xff, 0xff, 0xff, 0xff, 0xff, 0xff, 0xff, 
	0xff, 0xff, 0xff, 0xff, 0xff, 0xff, 0xff, 0xff, 0xff, 0xff, 0xff, 0xff, 0xff, 0xff, 0xff, 0xff, 
	0xff, 0xff, 0xff, 0xff, 0xff, 0xff, 0xff, 0xff, 0xff, 0xff, 0xff, 0xff, 0xff, 0xff, 0xff, 0xff, 
	0xff, 0xff, 0xff, 0xff, 0xff, 0xff, 0xff, 0xff, 0xff, 0xff, 0xff, 0xff, 0xff, 0xff, 0xff, 0xff, 
	0xff, 0xff, 0xff, 0xff, 0xff, 0xff, 0xff, 0xff, 0xff, 0xff, 0xff, 0xff, 0xff, 0xff, 0xff, 0xff, 
	0xff, 0xff, 0xff, 0xff, 0xff, 0xff, 0xff, 0xff, 0xff, 0xff, 0xff, 0xff, 0xff, 0xff, 0xff, 0xff, 
	0xff, 0xff, 0xff, 0xff, 0xff, 0xff, 0xff, 0xff, 0xff, 0xff, 0xff, 0xff, 0xff, 0xff, 0xff, 0xff, 
	0xff, 0xff, 0xff, 0xff, 0xff, 0xff, 0xff, 0xff, 0xff, 0xff, 0xff, 0xff, 0xff, 0xff, 0xff, 0xff, 
	0xff, 0xff, 0xff, 0xff, 0xff, 0xff, 0xff, 0xff, 0xff, 0xff, 0xff, 0xff, 0xff, 0xff, 0xff, 0xff, 
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
};
 
const unsigned char bitmap2 [] PROGMEM = {
	// 'display_2, 240x135px
	0xff, 0xff, 0xff, 0xff, 0xff, 0xff, 0xff, 0xff, 0xff, 0xff, 0xff, 0xff, 0xff, 0xff, 0xff, 0xff, 
	0xff, 0xff, 0xff, 0xff, 0xff, 0xff, 0xff, 0xff, 0xff, 0xff, 0xff, 0xff, 0xff, 0xff, 0xff, 0xff, 
	0xff, 0xff, 0xff, 0xff, 0xff, 0xff, 0xff, 0xff, 0xff, 0xff, 0xff, 0xff, 0xff, 0xff, 0xff, 0xff, 
	0xff, 0xff, 0xff, 0xff, 0xff, 0xff, 0xff, 0xff, 0xff, 0xff, 0xff, 0xff, 0xff, 0xff, 0xff, 0xff, 
	0xff, 0xff, 0xff, 0xff, 0xff, 0xff, 0xff, 0xff, 0xff, 0xff, 0xff, 0xff, 0xff, 0xff, 0xff, 0xff, 
	0xff, 0xff, 0xff, 0xff, 0xff, 0xff, 0xff, 0xff, 0xff, 0xff, 0xff, 0xff, 0xff, 0xff, 0xff, 0xff, 
	0xff, 0xff, 0xff, 0xff, 0xff, 0xff, 0xff, 0xff, 0xff, 0xff, 0xff, 0xff, 0xff, 0xff, 0xff, 0xff, 
	0xff, 0xff, 0xff, 0xff, 0xff, 0xff, 0xff, 0xff, 0xff, 0xff, 0xff, 0xff, 0xff, 0xff, 0xff, 0xff, 
	0xff, 0xff, 0xff, 0xff, 0xff, 0xff, 0xff, 0xff, 0xff, 0xff, 0xff, 0xff, 0xff, 0xff, 0xff, 0xff, 
	0xff, 0xff, 0xff, 0xff, 0xff, 0xff, 0xff, 0xff, 0xff, 0xff, 0xff, 0xff, 0xff, 0xff, 0xff, 0xff, 
	0xff, 0xff, 0xff, 0xff, 0xff, 0xff, 0xff, 0xff, 0xff, 0xff, 0xff, 0xff, 0xff, 0xff, 0xff, 0xff, 
	0xff, 0xff, 0xff, 0xff, 0xff, 0xff, 0xff, 0xff, 0xff, 0xff, 0xff, 0xff, 0xff, 0xff, 0xff, 0xff, 
	0xff, 0xff, 0xff, 0xff, 0xff, 0xff, 0xff, 0xff, 0xff, 0xff, 0xff, 0xff, 0xff, 0xff, 0xff, 0xff, 
	0xff, 0xff, 0xff, 0xff, 0xff, 0xff, 0xff, 0xff, 0xff, 0xff, 0xff, 0xff, 0xff, 0xff, 0xff, 0xff, 
	0xff, 0xff, 0xff, 0xff, 0xff, 0xff, 0xff, 0xff, 0xff, 0xff, 0xff, 0xff, 0xff, 0xff, 0xff, 0xff, 
	0xff, 0xff, 0xff, 0xff, 0xff, 0xff, 0xff, 0xff, 0xff, 0xff, 0xff, 0xff, 0xff, 0xff, 0xff, 0xff, 
	0xff, 0xff, 0xff, 0xff, 0xff, 0xff, 0xff, 0xff, 0xff, 0xff, 0xff, 0xff, 0xff, 0xff, 0xff, 0xff, 
	0xff, 0xff, 0xff, 0xff, 0xff, 0xff, 0xff, 0xff, 0xff, 0xff, 0xff, 0xff, 0xff, 0xff, 0xff, 0xff, 
	0xff, 0xff, 0xff, 0xff, 0xff, 0xff, 0xff, 0xff, 0xff, 0xff, 0xff, 0xff, 0xff, 0xff, 0xff, 0xff, 
	0xff, 0xff, 0xff, 0xff, 0xff, 0xff, 0xff, 0xff, 0xff, 0xff, 0xff, 0xff, 0xff, 0xff, 0xff, 0xff, 
	0xff, 0xff, 0xff, 0xff, 0xff, 0xff, 0xff, 0xff, 0xff, 0xff, 0xff, 0xff, 0xff, 0xff, 0xff, 0xff, 
	0xff, 0xff, 0xff, 0xff, 0xff, 0xff, 0xff, 0xff, 0xff, 0xff, 0xff, 0xff, 0xff, 0xff, 0xff, 0xff, 
	0xff, 0xff, 0xff, 0xff, 0xff, 0xff, 0xff, 0xff, 0xff, 0xff, 0xff, 0xff, 0xff, 0xff, 0xff, 0xff, 
	0xff, 0xff, 0xff, 0xff, 0xff, 0xff, 0xff, 0xff, 0xff, 0xff, 0xff, 0xff, 0xff, 0xff, 0xff, 0xff,
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

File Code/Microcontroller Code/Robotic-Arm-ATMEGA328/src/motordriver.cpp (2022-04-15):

#include <Arduino.h>
#include <AccelStepper.h>
#include "Main_Header.h"

#define nema17 0.5555
#define nema11_gearbox 28.333
#define nema17_gearbox 55.5555
#define nema11 0.5555
#define speed_value 2000
boolean state1 = false;
boolean state2 = false;
boolean state3 = false;
boolean state4 = false;
boolean state5 = false;
boolean state6 = false;


int get_speed(){
 int speed = speed_value;
 return speed;
}


//this works so bad need to rework with non blocking and simultaneous code --> fixed
void driveMotor(Motor motor1, Motor motor2, Motor motor3, Motor motor4, Motor motor5, Motor motor6){

AccelStepper stepper1 = AccelStepper(motor1.dir_pin, motor1.speed_pin, motor1.motorInterfaceType);
stepper1.setMaxSpeed(speed_value);
stepper1.setAcceleration(50);
AccelStepper stepper2 = AccelStepper(motor2.dir_pin, motor2.speed_pin, motor2.motorInterfaceType);
stepper2.setMaxSpeed(speed_value);
stepper2.setAcceleration(50);
AccelStepper stepper3 = AccelStepper(motor2.dir_pin, motor3.speed_pin, motor3.motorInterfaceType);
stepper3.setMaxSpeed(speed_value);
stepper3.setAcceleration(50);
AccelStepper stepper4 = AccelStepper(motor3.dir_pin, motor4.speed_pin, motor4.motorInterfaceType);
stepper4.setMaxSpeed(speed_value);
stepper4.setAcceleration(50);
AccelStepper stepper5 = AccelStepper(motor4.dir_pin, motor5.speed_pin, motor5.motorInterfaceType);
stepper5.setMaxSpeed(speed_value);
stepper5.setAcceleration(50);
AccelStepper stepper6 = AccelStepper(motor5.dir_pin, motor6.speed_pin, motor6.motorInterfaceType);
stepper6.setMaxSpeed(speed_value);
stepper6.setAcceleration(50);

Serial.print("Motor go ehhhhhh: ");

int motor1_steps = (motor1.moveto) * nema17;
int motor2_steps = (motor2.moveto) * nema17_gearbox;
int motor3_steps = (motor3.moveto) * nema17_gearbox;
int motor4_steps = (motor4.moveto) * nema11_gearbox;
int motor5_steps = (motor5.moveto) * nema11_gearbox;
int motor6_steps = (motor5.moveto) * nema11;

int arr[6] = {motor1_steps,motor2_steps,motor3_steps,motor4_steps,motor5_steps,motor6_steps};
int max = 0;

for (int i = 5; i >= 0; i--)
{
  if(max < arr[i]){
    max = arr[i];
  }
}

int counter = 0;
int counter_1 = 0;

while(counter < max){

  if(counter < motor1_steps){
    stepper1.move(1);
  }

  if(counter < motor2_steps){
    stepper2.move(1);
  }

  if(counter < motor3_steps){
    stepper3.move(1);
  }

  if(counter < motor4_steps){
    stepper4.move(1);
  }

  if(counter < motor5_steps){
    stepper5.move(1);
  }

  if(counter < motor6_steps){
    stepper6.move(1);
  }


  if(counter_1 == 2000){
      Serial.print(".");
      counter_1 = 0;
  }
  
  counter++;
  counter_1++;
}

 Serial.println(" ");
 Serial.println("Motor go chilling");
}

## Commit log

2022-01-16 Added Main Controller to Github
    [BOM_PartType-Robotic-Arn-Controller.xlsx]
2022-01-16 Added Stepper Controller to Github
    [BOM_PartType-Stepper-Motor Driver.xlsx]
2022-01-21 Created and added 17HS15-1684S-HG100 100:1 Ratio High Torgue Stepper motor
    [17HS15-1684S-HG100 v6.f3z]
2022-01-21 Updatet 17HS4401
    [17HS4401.f3d]
2022-01-21 Updatet Roboter Arm Combined
2022-01-21 Added Step_MD to Github
    [STEP_Motor_Driver.step]
2022-01-22 Added 17HS15 Stepper Motor + Reducer
2022-01-23 ↓ Updatet ReadMe 3D-Model to new Version of Arm
2022-01-25 Main Controller Routing New Alingment
    [PCB2.xls]
2022-01-25 Updated Ground Polygon
2022-01-25 Updated ReadMe to new Silkscreen
2022-01-28 Version 83 of Robot Arm
    Added Covers for the pulleys
2022-01-28 Added Improved Gerber Files for Manufacturing
    [PCB2.DRL, PCB2.GBL, PCB2.GBO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]
2022-01-28 added new Motor renders and small changes to rm
2022-01-29 Added V0.4 Main Controller improved Manufacturing Outputs
    [PCB2.GBL, PCB2.GBO, PCB2.GBP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]
2022-01-29 Added V0.2 Motor Controller improved Manufacturing Outputs
    [SteppperController.GBL, SteppperController.GBO, SteppperController.GBP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]
2022-01-30 Added Price Lists
    [Robot_Arm_Main_Controller.xlsx]
2022-01-30 Checked and updated Parts Chip shortage 2022
    [PCB2.GBL, PCB2.GBO, PCB2.GBP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]
2022-01-30 Added Stepper Motor Price List
    [Stepper_Motor_Controller.xlsx]
2022-02-02 Added improved Main Controller 3D-Model
    [Main-Controller-PCB.f3d]
2022-02-03 Added STLS for Manufacturing 3D-Models
    [Arm1.stl, Arm2.stl, Base-Cover.stl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]
2022-02-05 Added Nema 11 Stepper-Motor-Controller
    [BOM_PartType-Stepper-Motor Driver.xlsx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]
2022-02-05 added real nema 17 controller
    [BOM_PartType-Stepper-Motor Driver Nema 11.xlsx, BOM_PartType-Stepper-Motor Driver.xlsx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]
2022-02-05 Added Nema11 Motor-Controller Price List
    [Stepper_Motor_Controller_Nema11.xlsx]
2022-02-05 Added 11HS20-0674S-PG51 Stepper Motor
    [11HS20-0674S-PG51 .f3d]
2022-02-06 Added Version 0.132 Robotic-Arm
    [Arm1.step, Arm1.stl, Arm2.step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]
2022-02-08 Updated Motor Controller to Version 0.2.4
    [SteppperController.GBL, SteppperController.GBO, SteppperController.GBP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]
2022-02-19 Added/Updated Full Price List
    [Roboter Arm Price List.xlsx]
2022-02-20 added version 0.150 Robot Arm
2022-02-26 Changed Arm 4,5
    [Arm4.stl, Arm5.stl]
2022-02-27 Updated to V1.0 Robot Arm Report
2022-03-01 changes on price list
    [Roboter Arm Price List.xlsx]
2022-03-03 added styles to mode switch
2022-03-03 added js to switch mode
2022-03-03 button fix
2022-03-03 base changed
    [Base.stl]
2022-03-03 added power symbols
2022-03-05 commit for git
    [Arm4.stl]
2022-03-05 added voltage and speed divs
2022-03-05 added pause/stop/start buttons
2022-03-05 added side buttons
2022-03-07 added loader js
    [11HS20-0674S-PG51 v3.step, 11HS20-0674S-PG51 v3.stl]
2022-03-10 add remove buttons scaled
2022-03-11 fixe issues on model
    [Arm2.stl, Front.stl]
2022-03-12 price list
    [Roboter Arm Main Controller.xlsx, Stepper_Motor_Controller.xlsx, Stepper_Motor_Controller_Nema11.xlsx]
2022-03-12 changed gerbers and price list
    [PCB2.GBL, PCB2.GBO, PCB2.GBP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]
2022-03-13 added esp32 wireless features
    [Arm2.stl]
2022-03-15 testing wireless esp32
2022-03-16 changed arm 4 and 5
    [Arm4.stl, Arm5.stl]
2022-03-18 testing esp32 to website
2022-03-19 changed gerbers
    [BOM_PartType-Robotic-Arn-Controller.xlsx, BOM_PartType-Stepper-Motor Driver Nema 11.xlsx, BOM_PartType-Stepper-Motor Driver.xlsx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]
2022-03-19 fixed arm 1 and 2
    [Arm1.stl, Arm2.stl]
2022-03-20 panel gerber and base motor changed
2022-03-20 esp32 web client
2022-03-21 added motor programm
2022-03-22 pcb updated
2022-03-22 small changes to main esp32 code
2022-03-22 implemented motor class
2022-03-24 covers updated
    [Arm4_Cover.stl, Cover.stl, Cover2.stl]
2022-03-26 added inverse kinematic test
2022-03-27 changes to stls
    [Arm4.stl, Front.stl, Gear1.stl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]
2022-03-27 fixing inverse kinematics
2022-04-02 bug fixes and additions to atmega cpp
    [main.cpp, motordriver.cpp]
2022-04-03 maybe fixed display code
    [main.cpp]
2022-04-04 webserver 1.0
    [Arm4.stl, Arm4_Cover.stl, Cover.stl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]
2022-04-04 fixed esp32 code structure
    [Robotic_Arm_Webserver.cpp, main.cpp]
2022-04-09 changes to eoat and front
    [Front.stl, Gear1.stl, Gear2.stl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]
2022-04-11 reworked code at atmega
    [main.cpp, motordriver.cpp]
2022-04-12 fixed motor drivers, added images, changed model
    [Arm1.stl, Arm2.stl, Motor_Base.stl]
2022-04-15 renders, added SPI to ESP32
    [Arm1.stl]
2022-04-17 fixed display code and modell
    [Arm1.stl, Arm2.stl]
2022-04-21 changes to esp32 main and webserver
2022-04-24 changes to modell
    [Arm2.stl, Arm5.stl, Gear1.stl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]
2022-04-26 changes to SPI
2022-05-02 changed 3d modell
    [Base.stl, Front.stl]
2022-05-03 added Led Ring Code
    [Front.stl]
2022-05-15 added laser cutter files
    [Base_1_Laser_cutter.dwg, Base_2_Laser_cutter.dwg, Cover_Motors_2_Laser_cutter.dwg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]
2022-06-21 a lot of updates
    [Arm1.stl, Arm2.stl, Arm3.stl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]
2022-07-01 finall commit Won Technicus Award 2022
    [11HS20-0674S-PG51 .f3d, 11HS20-0674S-PG51 v3.step, 11HS20-0674S-PG51.f3d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]
